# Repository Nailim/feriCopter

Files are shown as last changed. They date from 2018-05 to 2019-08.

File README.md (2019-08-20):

# feriCopter

Model and 3D printing resources for student project.

### What is it?

Specialized quadcopter frame designed around STM32F3Discovery development board with ease of assembly in mind.
Assembly video for the project can be found on [YouTube](https://youtu.be/s-TGnOwG-w0).

## Content

- `blender/` - 3D model of the frame
- `meta/` - FreeCAD project for the documentation/assembly handout
- `stl/` - 3D printer ready STL files
- `feriCopter_assembly.pdf` - documentation/assembly handout

## Board Compatibility

Currently feriCopter supports the following boards:
- STM32F3DISCOVERY with `STM32F303VC` MCU
- STM32F411EDISCOVERY with `STM32F411VE` MCU

Frame compatibility for both targets is in the same Blender project, with the only change being the toggle of following modifiers on `Frame` object:
- `Boolean_cutout_pins_1_f3`
- `Boolean_cutout_pins_1_f411`

STL files are exported and corrected for both variants.

## Notes

Blender project contains base parts of the frame, however they were merged into `Frame`/`MotorMount` objects and further modified. Base objects are there for reference when needed, but should not be used for further editing.

## Parts

- Motors (Brushless, 2300 KV, ~30g):
  - 2x [Clockwise](https://hobbyking.com/en_us/brushless-motor-d2205-2300kv-cw.html)
  - 2x [Counter-Clockwise](https://hobbyking.com/en_us/brushless-motor-d2205-2300kv-ccw.html)
- 4x Electronic Speed Controller (~12 A): [Multistar 32bit](https://hobbyking.com/en_us/multistar-32bit-12a-0-lite.html) or [Multistar Mini](https://hobbyking.com/en_us/mini-blheli-multi-12a-opto.html)
- 1x [Power Distribution Board](https://hobbyking.com/en_us/pdb-xt60-w-bec-5v-12v.html)
- 4x [Propeller (2x Clockwise, 2x Counter-Clockwise, ~10 cm)](https://hobbyking.com/en_us/dys-t4045-r-4x4-5-cw-ccw-pair-2-pairs-pack-red.html)
- 2x [Gold Connectors (2mm, 2x 10 pairs)](https://hobbyking.com/en_us/2mm-gold-connectors-10-pairs-20pc-1.html)
- 1x [Radio Control System (Controller)](https://hobbyking.com/en_us/i6s-afhds-2a-white-mode2-6ch-radio-with-colour-box.html)
- 1x LiPo Battery (14.8V, 45C, 1300 mAh, 4S1P)
- 1x Velcro (Battery attachment)
- 1x [LiPo Charger](https://hobbyking.com/en_us/turnigy-e3-compact-2s-3s-lipo-charger-100-240v-us-plug.html)
- 1x [USB Simulator Cable (Controller PC Connection)](https://hobbyking.com/en_us/usb-simulator-cable-xtr-aerofly-fms.html)
- 1x [LiPo Bag](https://hobbyking.com/en_us/lithium-polymer-charge-pack-18x22cm-sack.html)

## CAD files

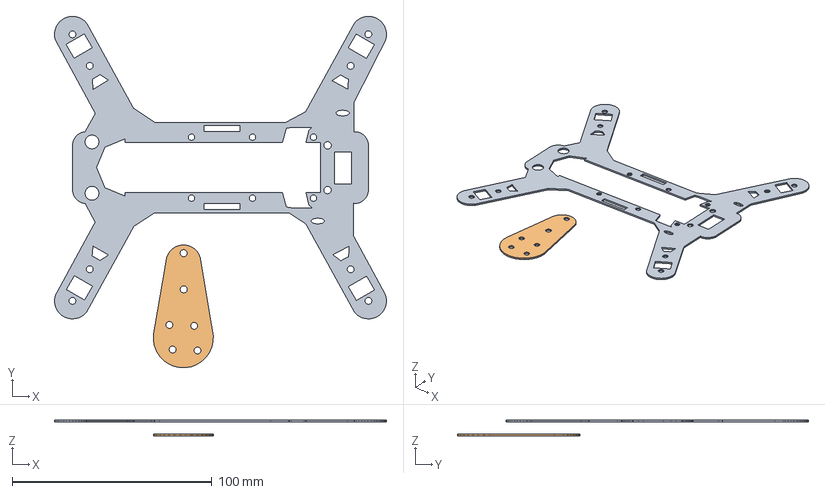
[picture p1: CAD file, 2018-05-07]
meta/feriCopter.fcstd
166.0 x 175.7 x 7.76 mm
Extrude_feriCopter
Extrude_feriCopter_motorMount

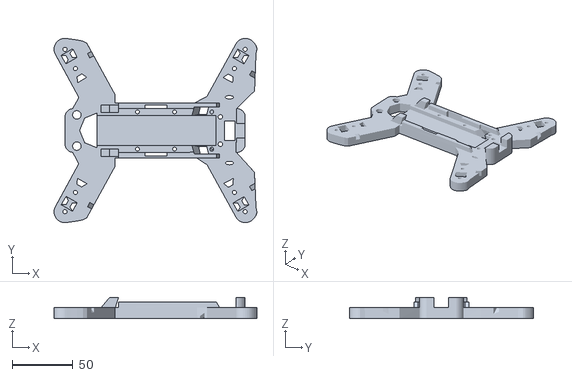
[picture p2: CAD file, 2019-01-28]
stl/feriCopter_final_f411.stl
166.6 x 151.3 x 17.5

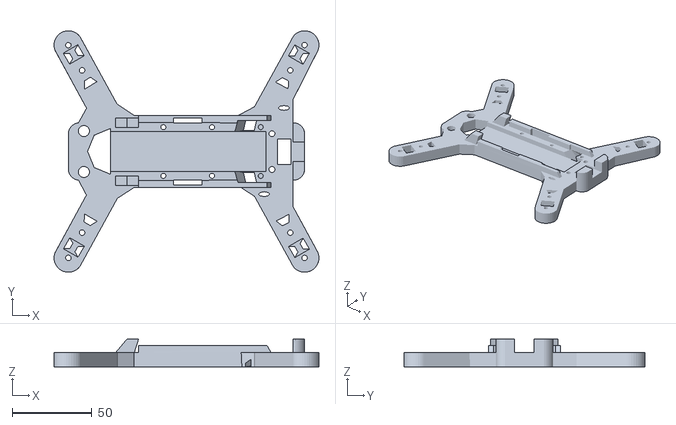
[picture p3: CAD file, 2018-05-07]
stl/feriCopter_final_original.stl
166.0 x 151.3 x 17.5

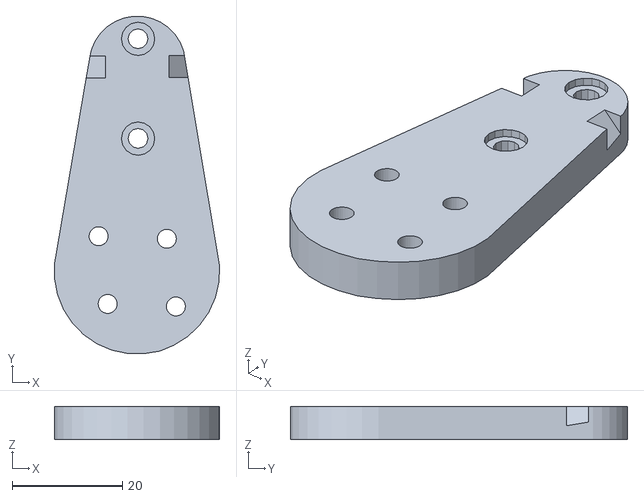
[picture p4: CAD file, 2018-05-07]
stl/feriCopter_motorMount_final.stl
30.0 x 61.3 x 6.00

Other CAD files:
stl/feriCopter_final_f3.stl
blender/feriCopter.blend

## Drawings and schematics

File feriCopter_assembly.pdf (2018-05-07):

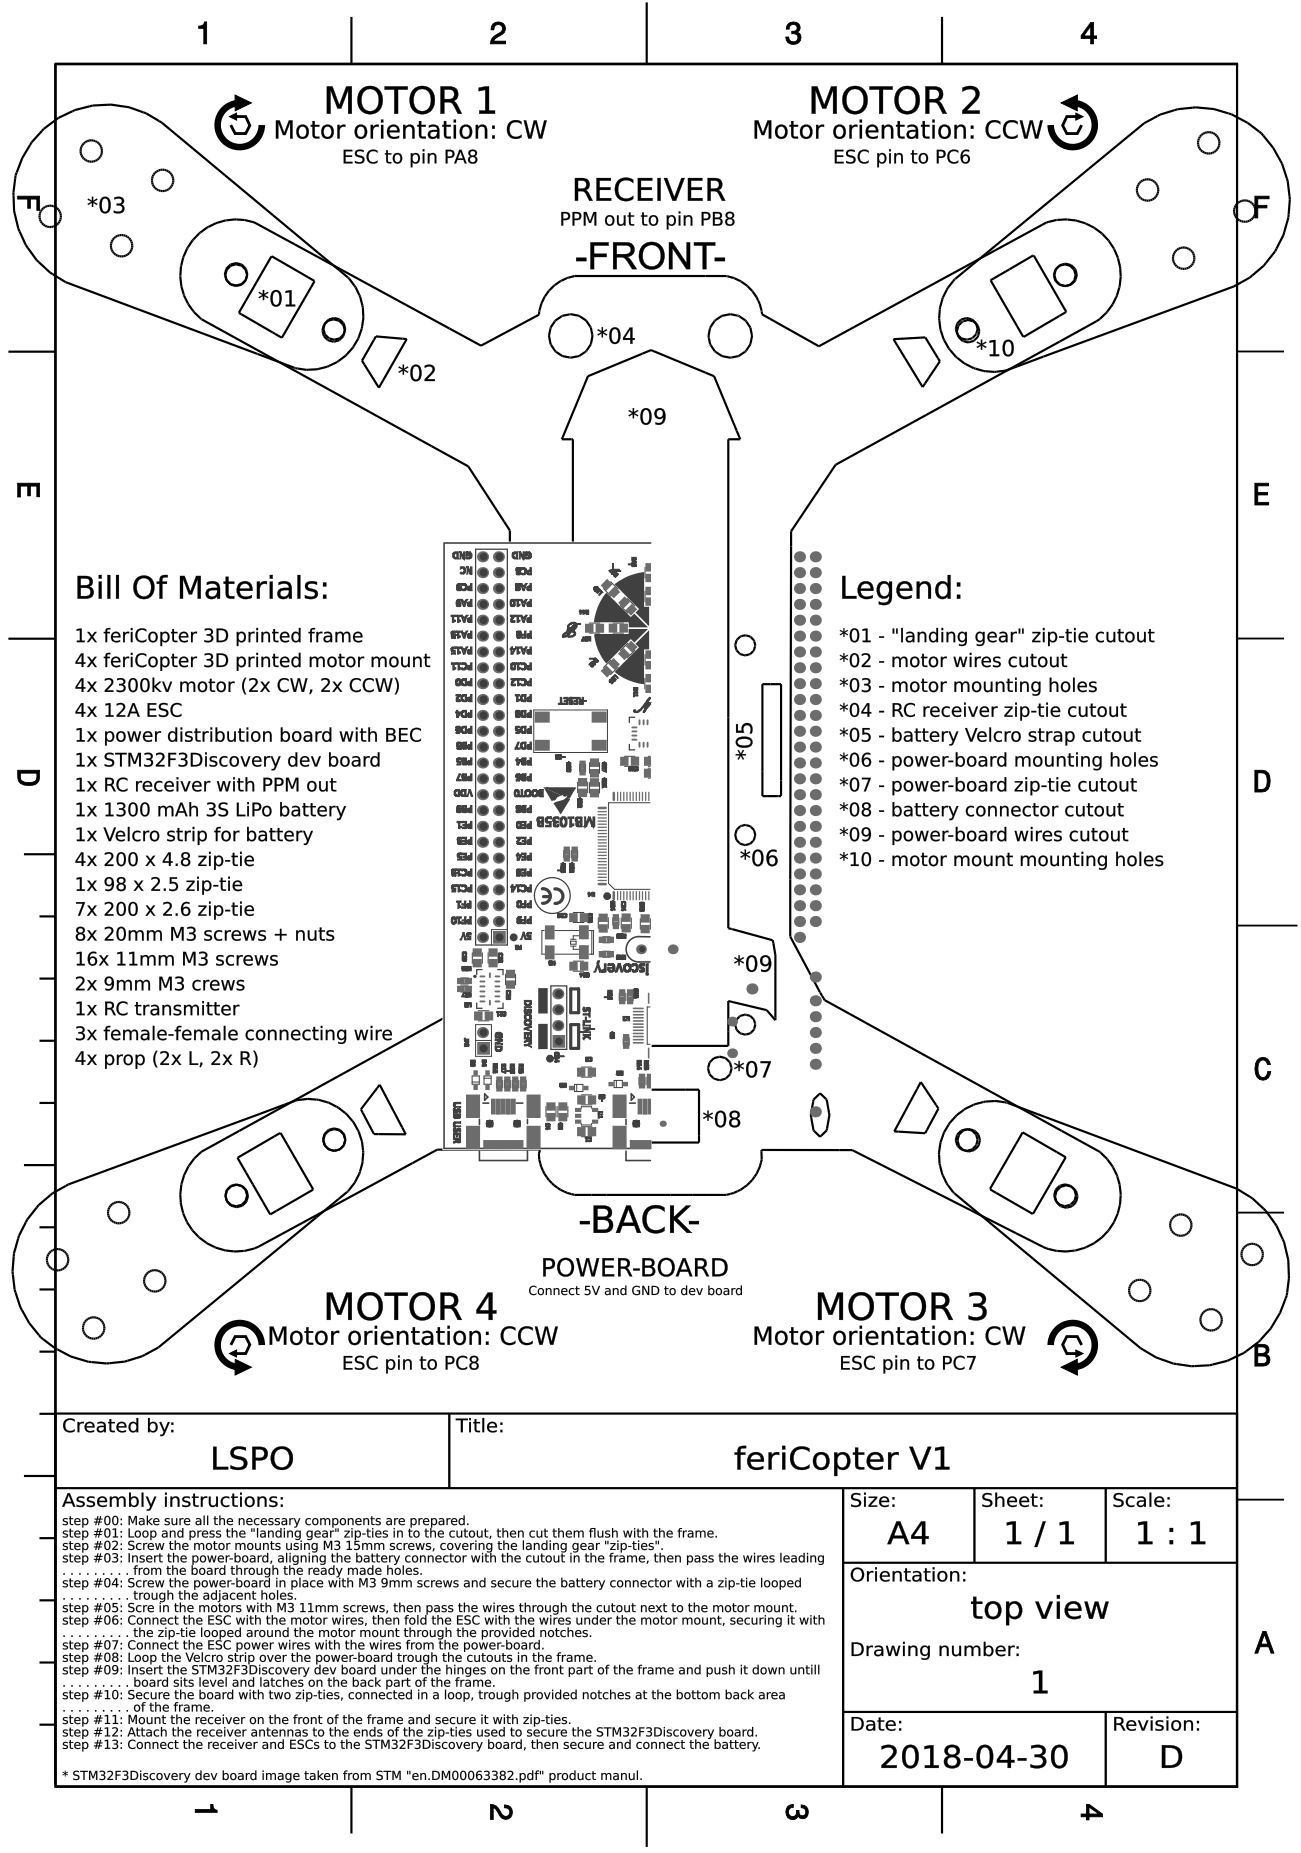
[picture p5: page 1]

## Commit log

2018-05-07 Initial feriCopterV1 commit
    [feriCopter.blend, feriCopter.fcstd, feriCopter_final.stl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]
2018-05-11 Capitalize STL in README.md
2019-01-27 Adapt F3 frame to fit F411, Improve frame rigidness (thicker 'legs'), Ignore Blender backup files in git
    Also made it a bit thicker on parts that were breaking often.
    [feriCopter.blend]
2019-01-27 Duplicate jumper pins cutout to support F3 and F411 through modifier toggles
    [feriCopter.blend]
2019-01-27 Export frame enhancements and F3/F411 compatibility to fixed STLs
    [feriCopter_final.stl, feriCopter_final_f3.stl, feriCopter_final_f411.stl]
2019-01-27 Add ziptie cutouts to extended frame 'legs'
    [feriCopter.blend, feriCopter_final_f3.stl, feriCopter_final_f411.stl]
2019-01-27 Expand README.md with board compatibility and Blender project notes
2019-01-28 Add back original frame
    [feriCopter_final_original.stl]
